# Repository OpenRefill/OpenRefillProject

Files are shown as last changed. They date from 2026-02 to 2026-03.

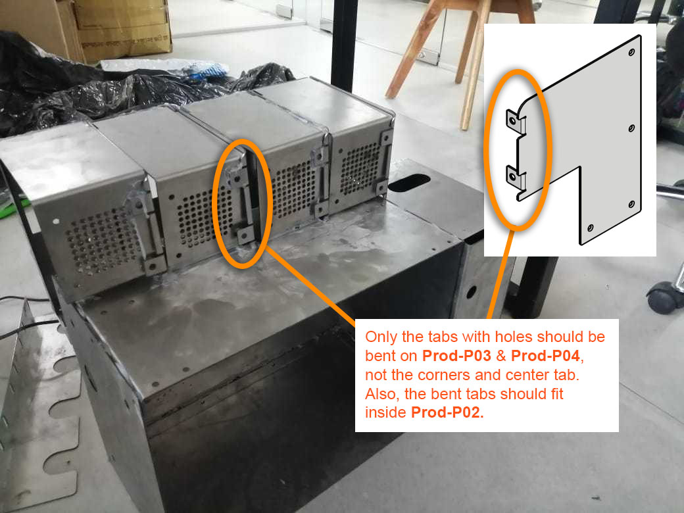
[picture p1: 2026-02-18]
Hardware Designs/Mechanical/Photos/img-20230101-wa0018 (with notes) copy.jpg

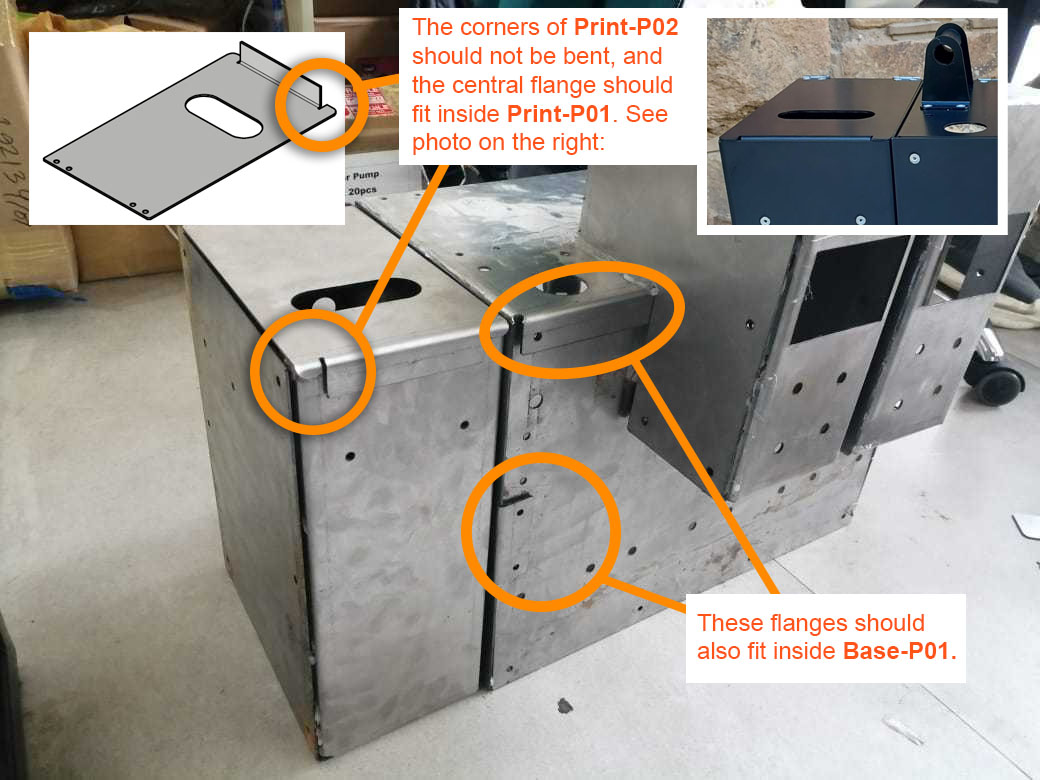
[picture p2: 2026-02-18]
Hardware Designs/Mechanical/Photos/img-20230101-wa0014 (with notes).jpg

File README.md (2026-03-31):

# OpenRefill 
An open-source platform for refill and reuse dispenser systems. 

## The Mission
We want to accelerate the shift away from single-use plastic by enabling open, low-cost refill dispensing systems, through open-source designs, shared standards, and collaboration. Our focus is on personal care products (shampoos, conditioners, soaps, etc) that are sold to developing markets in sachets. 

Find out more at [openrefill.com](https://openrefill.com) and dive deeper at our [research wiki](https://github.com/OpenRefill/OpenRefill/wiki/Research). 

## Getting started
1. Read the [licence notice](LICENCE-NOTICE.md) and understand your freedoms and responsibilities.
2. Read our [code of conduct](CODE_OF_CONDUCT.md) and our [contribution guidelines](CONTRIBUTING.md).
3. Check out our [discussions page](https://github.com/OpenRefill/OpenRefill/discussions). Feel free to introduce yourself in [Welcome to OpenRefill Discussions!](https://github.com/OpenRefill/OpenRefill/discussions/1#discussion-9450050).
4. Review our [open issues](https://github.com/OpenRefill/MainProject/issues) to start contributing.
5. Understand the logistics, operational, and business model dimensions of deploying a refill service by heading to [Refill Realities](https://www.refillrealities.com/#playbooks) and reading their playbooks. 

## Need help? 
- Email us at hello@openrefill.com.

## Follow Us 
[LinkedIn](https://www.linkedin.com/company/open-refill/?viewAsMember=true) 
#openrefill 
#refillrevolution

## Original Contributors

OpenRefill is a collaborative effort brought to life by industry leaders in smart logistics, digital innovation, and global sustainability:

* **[Smartfill](https://smartfill.store)** – A leading global supplier of smart dispensers and cloud-based logistics and inventory management for bulk products.
* **[DY|DX Digital](https://dydx.digital)** – A leading innovation consultancy.
* **[TRANSFORM](https://www.transform.global/home.html)** – A joint initiative between Unilever, the UK Foreign, Commonwealth & Development Office (FCDO), and EY.
* **[BOPINC](https://bopinc.org)** & **[Unilever Bangladesh](https://www.unilever.com.bd/)** – Strategic partners whose work on the **URefill** project provided foundational results for this initiative.
* **[Wizkit](https://www.linkedin.com/company/wizkitglobal/posts/?feedView=all)** - Wizkit supported the testing, deployment and maintenance of a fleet of machines in Dhaka stores during the initial **URefill pilots**.

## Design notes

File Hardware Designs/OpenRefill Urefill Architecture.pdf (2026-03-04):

# OpenRefill Technical Architecture:

## Urefill Version

2026/03/03

# Overview

The U-Refill cabinet contains 4 liquid personal care dispensers. Each dispenser has the following main components:
- 1x Peristaltic pump
- 1x LCD screen
- 4x Buttons
- 1x Trigger nozzle
- 1x Loadcell
- 1x Peripheral PCB

All the components are attached to the main cabinet, which consists of laser cut and bent metal parts. Some 3d-printed parts are also used, e.g., the button covers.

The dispenser functions as follows:
1. User selects an amount
2. User presses trigger button/nozzle upwards
3. The pump runs for a calibrated time period for the selected volume
4. A receipt is printed out.
5. The dispense event is sent to the cloud interface.

The dispenser load cell weighs the dispenser hopper (5L bottle or jerry can). The loadcell reading can be used to determine if the hopper is empty. Currently though the loadcell implementation is not functional and needs to be redesigned.

### Version History

This document pertains to the U-refill project version. A minor upgrade was manually made to improve the flow rate in 2024. Also an alternative and improved hopper bracket was designed, however not implemented during this time. The main PCB was also updated to include a ground plane. Previously it only had ground traces.

# Mechanical Components

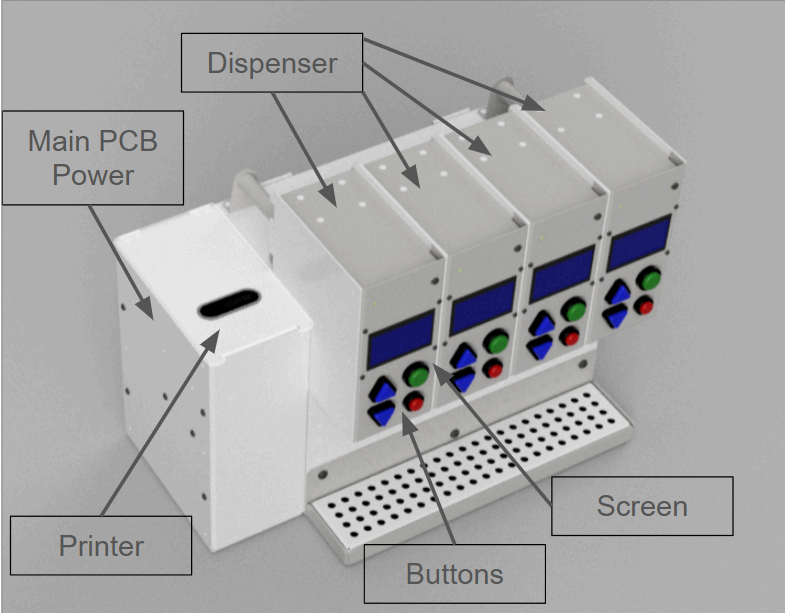
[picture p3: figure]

The cabinet has four dispensers, with a shared power supply, main PCB and printer.

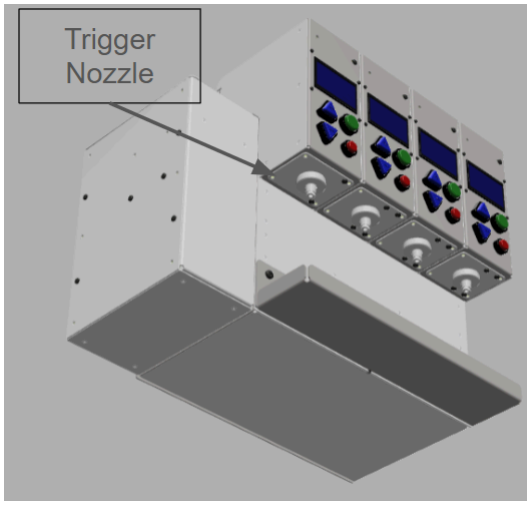
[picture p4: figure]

The trigger nozzle - this is pressed up to start dispensing after selecting an amount.

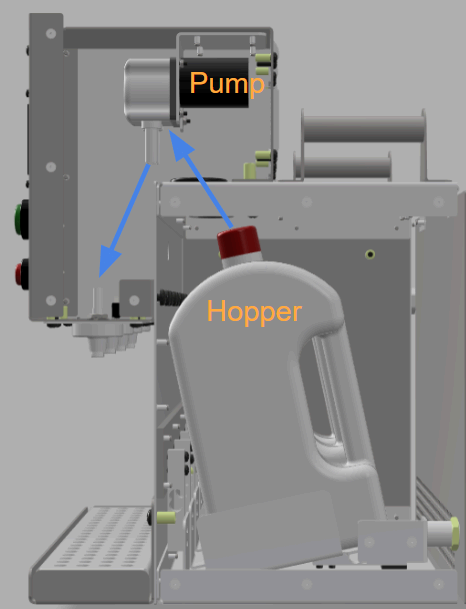
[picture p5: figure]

Side view of a dispenser. The hopper (5L jerrycan or bottle), contains the product supply. The motor pumps the liquid through the tube (blue arrows) to the Trigger Nozzle. Note this shows the updated design for the corrected load cell orientation.

# Electronics

The main PCB controls all four dispensers. The PCB has three ESP32 development boards. The boards communicate with each other using I2C.

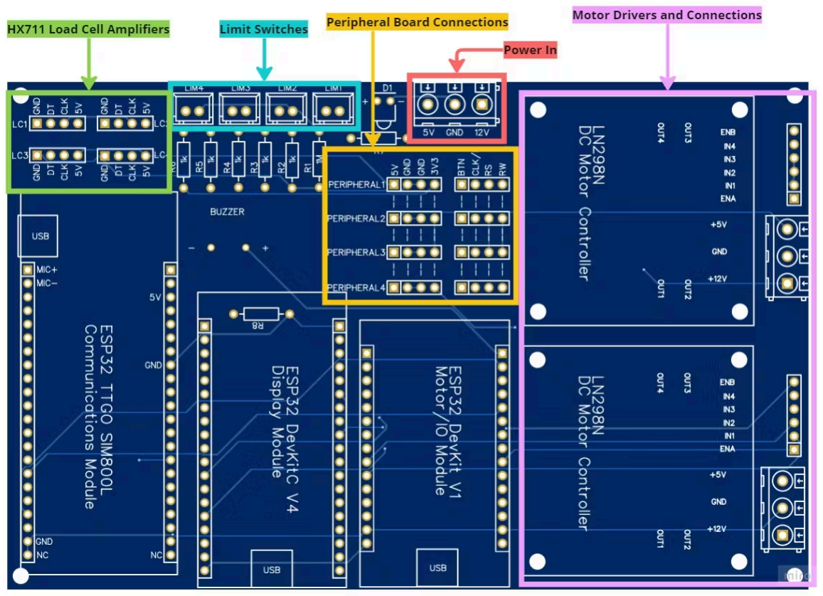
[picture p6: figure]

The main PCB with connection headers.

### Comms Module

Development Board: LILYGO TTGO T-Call V1.4 CH9102F QFN24 ESP32 Wireless Module GPRS Antenna SIM Card SIM800L Board

This ESP communicates with Azure-IoT-Central. The sim-card module mounted on it however does not work with the IoT/ESP internet library, and is not used. A WiFi router is used instead. Internet connection is used to send status updates and dispense events (records) to the cloud database. The current time is also obtained with NTP sync.

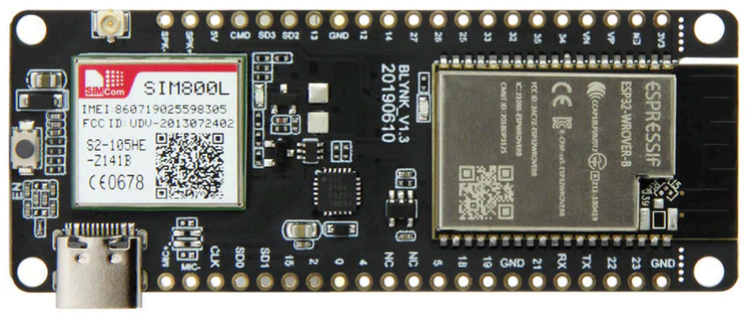
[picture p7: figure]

The LilyGo ESP module with SIM card slot

The loadcell ADC boards are also connected to this ESP. But as noted, the load cell circuit and mechanical orientation are not functional. The HX711 module (breakout board) is used to convert the load cell signal into a digital value using an ADC. The ADC digital output might need to be level shifted (5V to 3.3V).

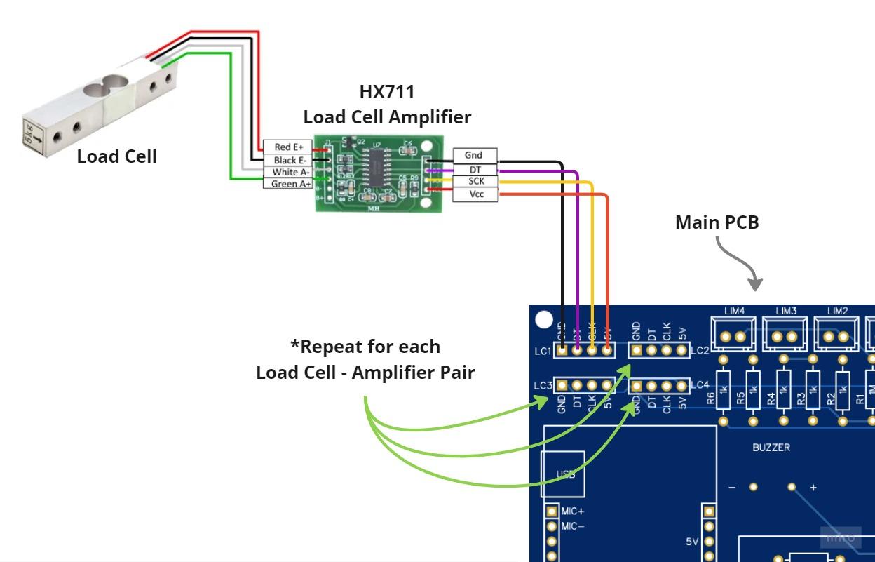
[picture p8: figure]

The loadcell connected to an HX711 loadcell ADC and amplifier, which is connected to the main PCB

### Display Module

Development Board: ESP32-WROOM32 DevKitC V4

This ESP drives all the displays. The display is a 128x64 LCD character display . Currently, the display is set to use only Bangladeshi characters.

The display module connects to each display with the Peripheral PCB.

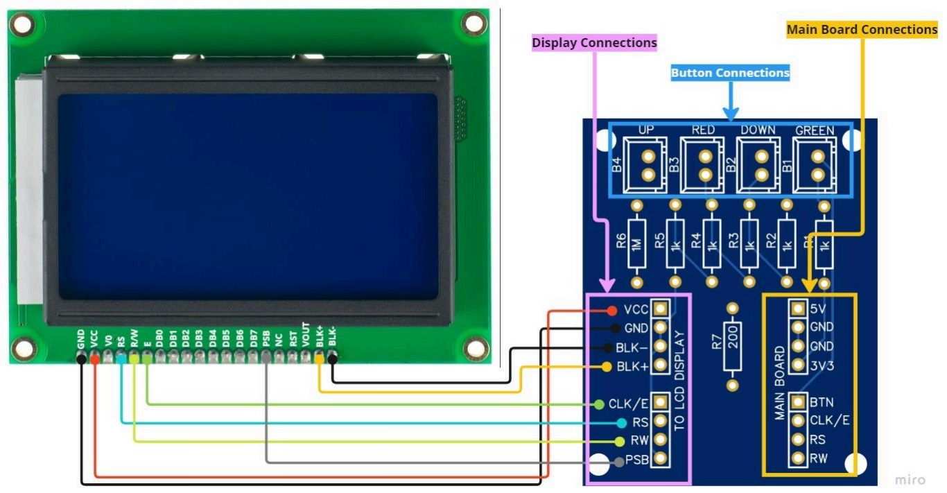
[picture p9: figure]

The display module connected to the peripheral PCB

### Main (Motor and IO) Module

Development Board: ESP32-WROOM32 DEVKIT V1

The main board does the following:
- Controls the four pump motors with DC motor drivers (also breakout boards).
- Check the buttons and trigger status of each dispenser. A resistor ladder is used to reduce the number of input pins required. All the buttons for one dispenser are connected to one pin. The voltage level as read with the ADC is used to determine if a specific button is pressed or not. The four nozzle-trigger buttons are also joined together using the same technique. The buttons are wired via the peripheral PCB to the main PCB.
- Control the buzzer.
- Connects to the Bluetooth printer to print receipts.

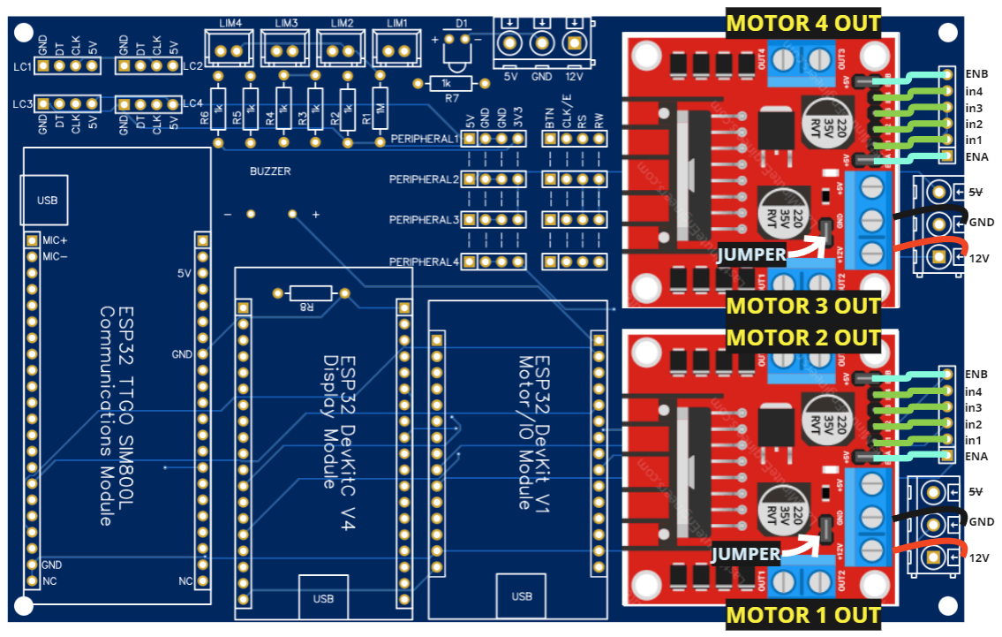
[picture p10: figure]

View of motor drivers mounted on the main PCB

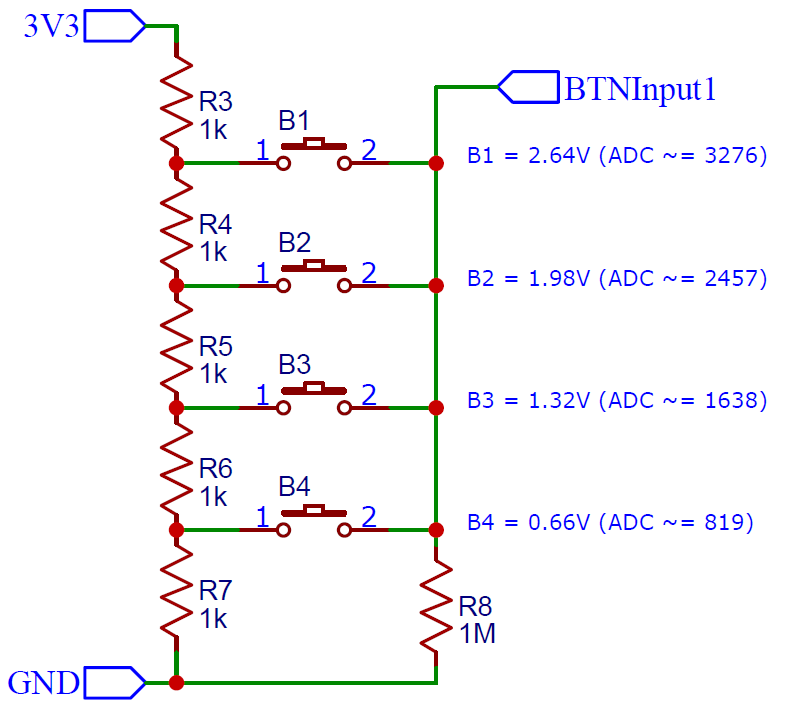
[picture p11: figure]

Voltage ladder used for buttons

### Pin Assignments: Peripheral PCB to Main Board

Pin Name | Pin Type | Description | Notes
5V | Power | 5V Power in
GND | Ground | Signal ground
3V3 | Analog Input | 3.3V reference for button circuit
BTN | Analog Output | Analog button voltage out
CLK/E | Serial Clock | Display clock
RS | Serial Data | Display chip select
R/W | Serial Data | Display data

### Pin Assignments: Peripheral to Display

Pin Name | Pin Type | Description | Notes
VCC | Power | 5V Power
GND | Ground | Signal ground
BLK- | Ground | Backlight cathode (-)
BLK+ | Power | Backlight anode (+)
CLK/E | Serial Clock | Display clock

RS | Serial Data | Display chip select
R/W | Serial Data | Display data
PSB | Digital Input | Parallel/Serial Bit (0=Serial)

## Power Supply

A 12V 10A (120W) power supply with battery connection is used to power the cabinet. A buck converter outputs the 5V power rail, which supplies the screens and ESP boards.

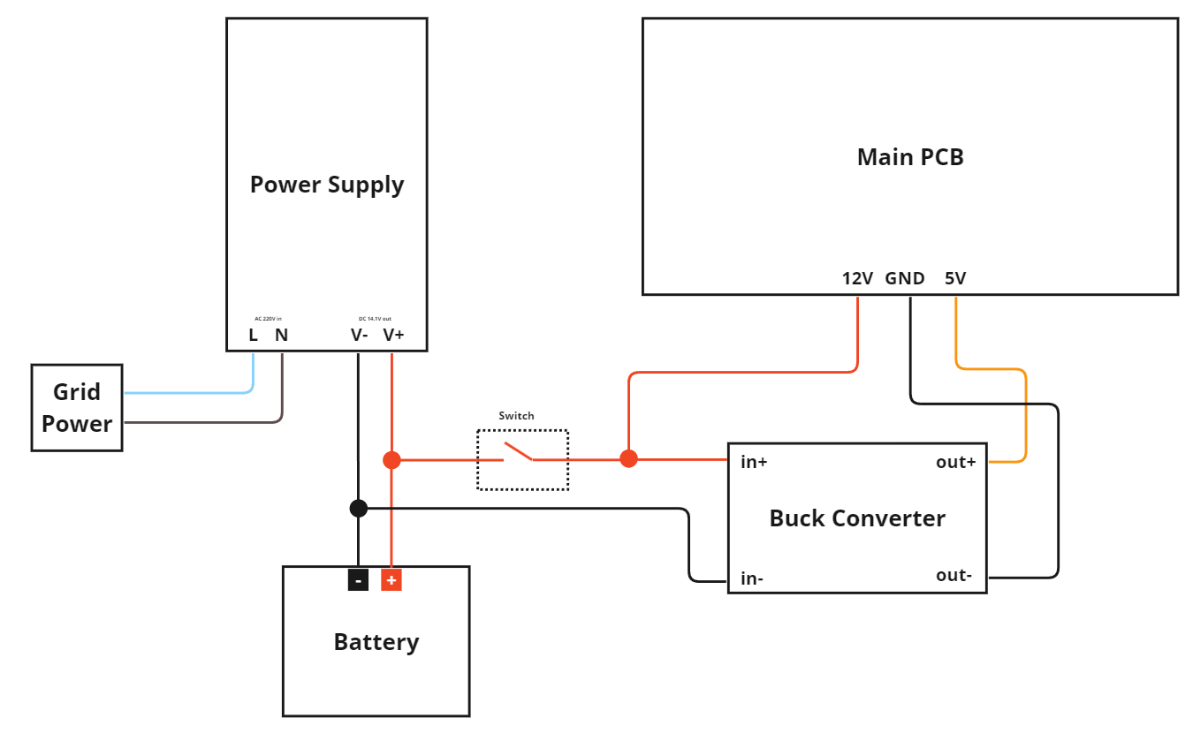
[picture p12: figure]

Block diagram of the power supply

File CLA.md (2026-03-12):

# OPENREFILL CONTRIBUTOR LICENCE AGREEMENT

Thank you for your interest in contributing to the OpenRefill project. 

To protect the project, its users, and the open-source community, Smartfill Ltd (UK company number 13799654) (**Smartfill**) requires all contributors to agree to this Contributor Licence Agreement before we can accept your contributions. 

This agreement ensures we have the necessary legal rights to distribute your contributions while you retain ownership of your original work. By submitting a contribution (for example, through a pull request, email, or issue tracker), you unconditionally and irrevocably agree to the following terms— 

## 1. DEFINITIONS 

1.1. **"You"** means the individual or legal entity submitting the Contribution; 

1.2. **"Contribution"** means any hardware design, software, firmware, documentation, or other material you submit to the OpenRefill project; and 

1.3. **"Project"** means the OpenRefill project, managed by Smartfill. 

## 2. GRANT OF RIGHTS 

You grant to Smartfill— 

2.1. a perpetual, worldwide, non-exclusive, royalty-free, irrevocable licence to reproduce, prepare derivative works of, publicly display, publicly perform, sublicense, and distribute your Contribution; and

2.2. a patent licence to make, have made, use, sell, offer for sale, and import your Contribution as incorporated into the Project.

## 3. YOUR RETAINED RIGHTS 

3.1. You retain all copyright and patent rights in your Contribution. 

3.2. This agreement does not prevent you from using your own Contribution for any other purpose or licensing it to others under different terms. 

## 4. OUTBOUND LICENSING 

Accepted Contributions may be distributed to the public under the project’s then-current opensource licensing framework (currently CERN-OHL-W-2.0, MPL-2.0, and CC-BY-SA-4.0). 

## 5. YOUR WARRANTIES 

By submitting a Contribution, you confirm and warrant— 

5.1. that you have the legal right to grant these licences; 

5.2. that the Contribution is your original creation, or you have sufficient rights and permissions from any third-party owners to make the submission and grant the rights in this agreement; and 

5.3. that, to the best of your knowledge, the Contribution does not include material subject to third-party licence terms that are inconsistent with the project’s open licensing framework (CERNOHL-W-2.0, MPL-2.0, and CC-BY-SA-4.0). 

## 6. DISCLAIMER OF WARRANTIES 

Except for the warranties stated in **Section 5** above, you provide your Contribution on an "AS IS" basis, without any additional warranties or conditions, express or implied. 

## 7. ACCEPTANCE:

By submitting a pull request or transferring project files to Smartfill, you explicitly accept and agree to the terms of this agreement.

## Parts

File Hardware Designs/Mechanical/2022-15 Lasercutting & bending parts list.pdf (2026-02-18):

Part Number | Part Title | Operation | Material | Material Thickness | Finish | QTY | Part Drawing No:
Base-P01 | Base Box Face | Cut | Mild steel | 1,6 | As supplied | 10 | 2022-15-D01
Base-P02 | Base Box Top | Cut, bend | Mild steel | 1,6 | As supplied | 10 | 2022-15-D02
Base-P03 | Base Box Bottom | Cut, bend | Mild steel | 1,6 | As supplied | 10 | 2022-15-D03
Base-P04 | Base Box Right | Cut, bend | Mild steel | 1,6 | As supplied | 10 | 2022-15-D04
Base-P05 | Base Box Left | Cut, bend | Mild steel | 1,6 | As supplied | 10 | 2022-15-D05
Base-P06 | Base Box Door | Cut | Mild steel | 1,6 | As supplied | 10 | 2022-15-D06
Base-P07 | Mounting Plate | Cut | Mild steel | 5,0 | As supplied | 10 | 2022-15-D07
Base-P08 | Alignment Bracket | Cut, bend | Mild steel | 1,6 | As supplied | 10 | 2022-15-D08
Base-P09 | Hopper Support | Cut, bend | Mild steel | 2,0 | As supplied | 40 | 2022-15-D09
Hand-P01 | Handle Bracket | Cut, bend | Mild steel | 1,6 | As supplied | 40 | 2022-15-D10
Noz-P03-1 | Nozzle Mount (Pin) | Cut | Mild steel | 1,6 | As supplied | 40 | 2022-15-D11
Noz-P04 | Switch Mount | Cut | Mild steel | 1,6 | As supplied | 40 | 2022-15-D13

### Dispenser Sheet Metal Cutting & Bending Parts List

Print-P01 | Printer Box Main | Cut, bend | Mild steel | 1,6 | As supplied | 10 | 2022-15-D14
Print-P02 | Printer Box Side | Cut | Mild steel | 1,6 | As supplied | 10 | 2022-15-D15
Print-P03 | Printer Box Top | Cut, bend | Mild steel | 1,6 | As supplied | 10 | 2022-15-D16
Print-P04 | Printer Bracket | Cut, bend | Mild steel | 2,0 | As supplied | 10 | 2022-15-D17
Prod-P01 | Product Box Face | Cut, bend | Mild steel | 1,6 | As supplied | 40 | 2022-15-D18
Prod-P02 | Product Box Cover | Cut, bend | Mild steel | 1,6 | As supplied | 40 | 2022-15-D19
Prod-P03 | Product Box Right | Cut, bend | Mild steel | 1,6 | As supplied | 40 | 2022-15-D20
Prod-P04 | Product Box Left | Cut, bend | Mild steel | 1,6 | As supplied | 40 | 2022-15-D21
Prod-P05 | Pump bracket | Cut, bend | Mild steel | 2,0 | As supplied | 40 | 2022-15-D22
Tray-P01 | Tray support | Cut, bend | 304 Stainless | 2,0 | Brushed | 10 | 2022-15-D24
Tray-P02 | Drip Cover | Cut, bend | 304 Stainless | 1,6 | Brushed | 10 | 2022-15-D25
Hand-P02 | Handle Tube | Cut | Mild steel, (round tube) | 1,6 | As supplied | 20 | 2022-15-D26
Base-P10 | Cam Lock Catch | Cut, bend | Mild steel, (round tube) | 2,0 | As supplied | 10 | 2022-15-D27

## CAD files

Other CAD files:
Hardware Designs/Mechanical/Drawings/DWG/Dispenser Overall Dimensions.dwg
Hardware Designs/Mechanical/Drawings/DWG/4 product dispenser unit -3.dwg
Hardware Designs/Mechanical/Drawings/DWG/Drip container - request for quotes.dwg
Hardware Designs/Mechanical/Drawings/DWG/Short printer box.dwg
Hardware Designs/Mechanical/Drawings/DWG/Other Parts Drawings.dwg
Hardware Designs/Mechanical/Drawings/DWG/Overview drawings D01-03.dwg
Hardware Designs/Mechanical/Drawings/DWG/external dimensions for cardboard.dwg
Hardware Designs/Mechanical/Drawings/DWG/Tall printer box.dwg

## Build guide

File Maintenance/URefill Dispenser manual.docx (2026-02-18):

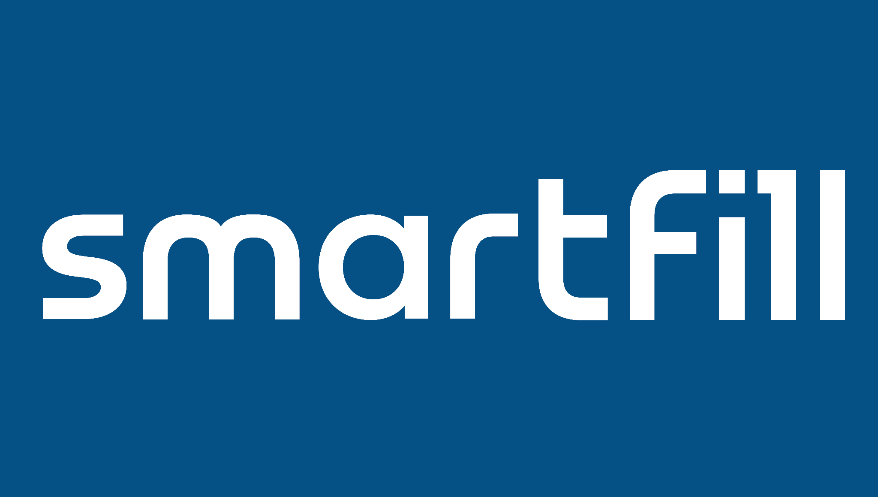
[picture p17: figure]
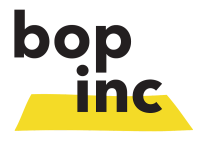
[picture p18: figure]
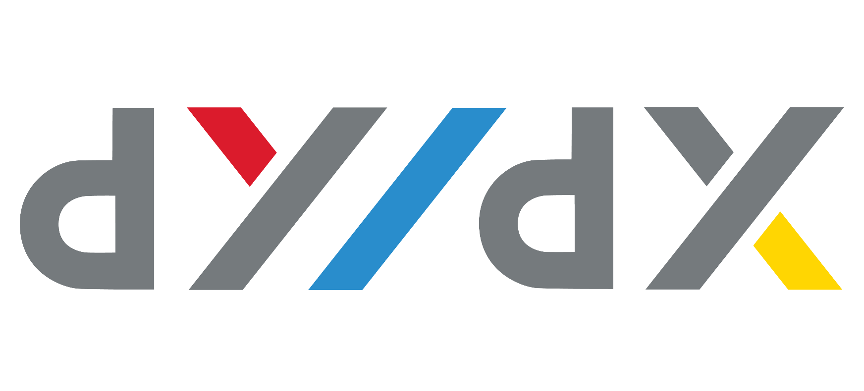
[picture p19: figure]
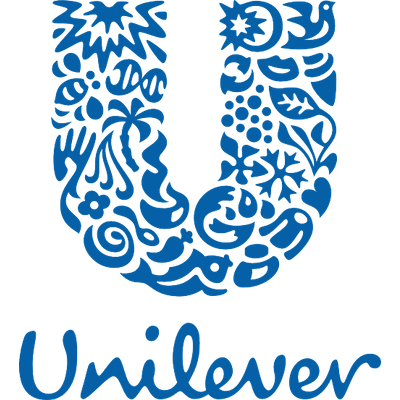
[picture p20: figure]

Bopinc

Personal Care Dispenser Manual

Version 1.0

05 December 2022

## Contents

Contents 2

Background 3

Dispenser Overview 3

Power supply 3

Measurements and Key Components 3

Dispensing Accuracy 5

Product Quality Assurances 5

Usage 5

Stock replenishment 7

Troubleshooting 8

## Background

The refill dispenser is an electronic machine that dispenses viscous liquid personal care products such as shampoo. Consumers use the machine to fill empty, reusable containers with product from the dispenser. The objective of the dispenser is to encourage shoppers to reduce the purchasing and use of personal care products in small plastic sachets which have become an environmental problem.

## Dispenser Overview

### Power supply

Electricity is required for the electronic refill dispenser to operate. There is no on/off switch for the dispenser and it automatically turns on once connected to a power supply, and off when there is no power supply. The machine is indicated as being on when the LCD screens show text and intermittently flash with light.

The dispenser has a standard cable and plug that plugs into the main grid electricity supply. In the case of brief periods of electricity loss, there is a battery that is able to power the dispenser for up to 4 hours of continual motor use, and it is charged by the main power supply.

### Measurements and Key Components

Front view

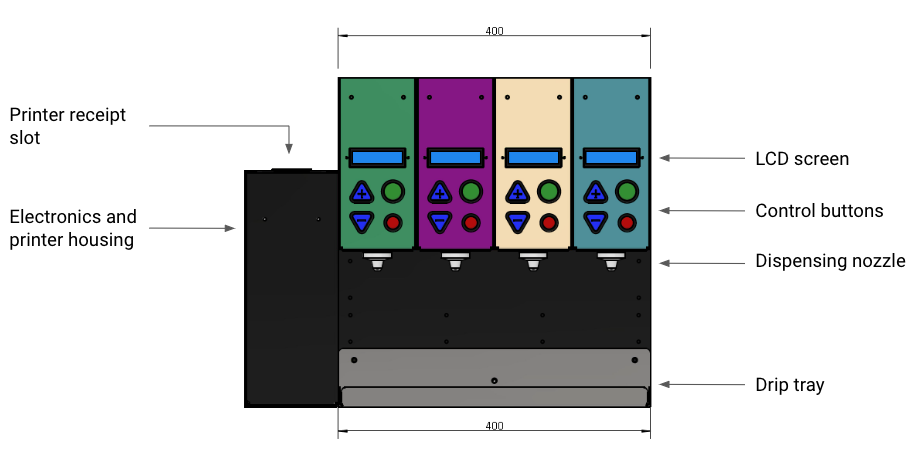
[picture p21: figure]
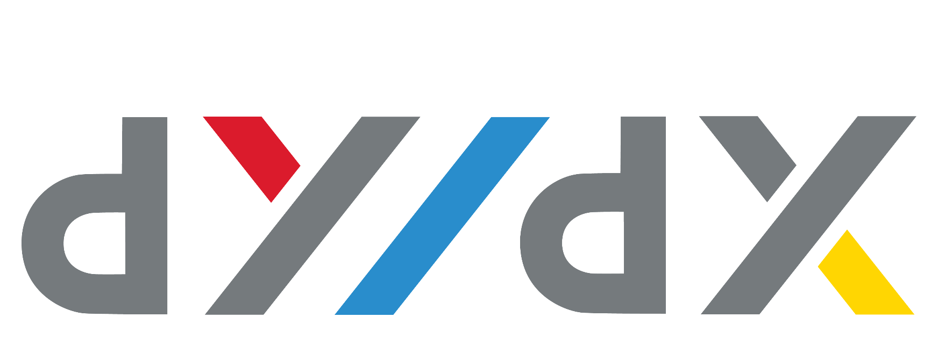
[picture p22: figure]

Side view

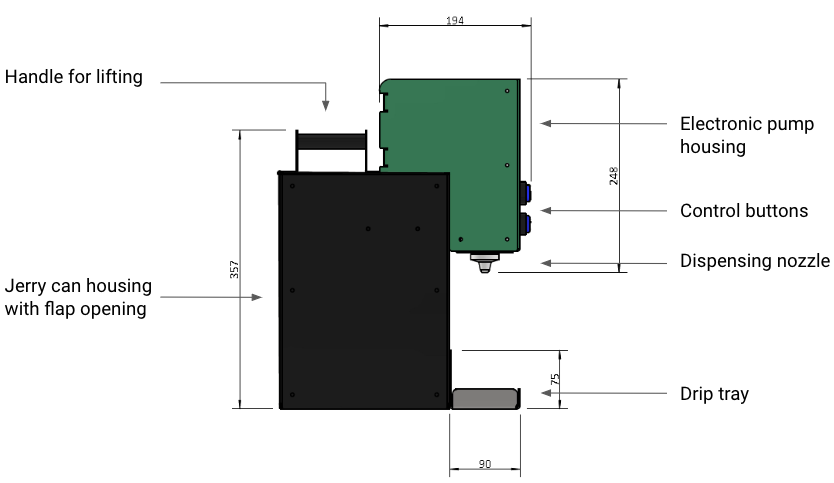
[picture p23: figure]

Internal view

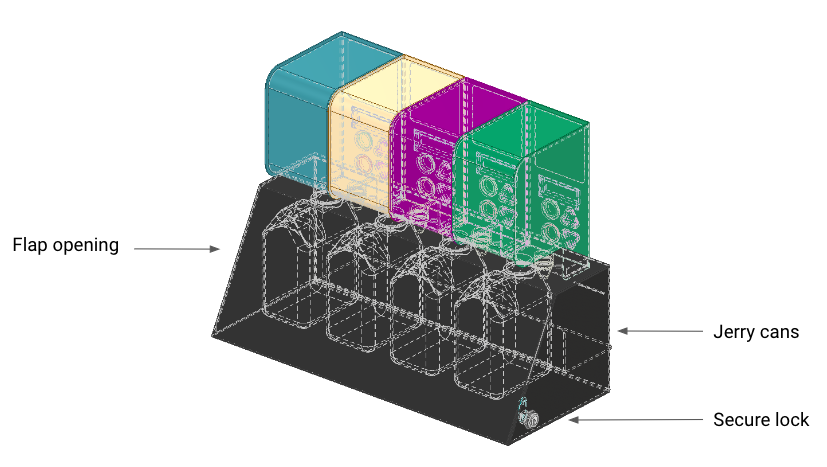
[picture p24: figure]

### Dispensing Accuracy

Because of the small quantities dispensed by the machine, the refill station is very accurate with an error margin of less than 3%. Any error will be positive (i.e. more product dispensed rather than less), so the customer gets at least the quantity they select.

### Product Quality Assurances

Product quality is maintained in 4 ways:

1. Jerry cans are securely contained within the dispenser itself, and access to the jerry cans are protected by lock and key. Only approved Unilever contacts have a key and are able to gain access to the jerry cans to protect the product from being tampered with.
2. Jerry cans are not exposed to UV as they are secured within the dispenser.
3. To avoid any microbial contamination or degradation of the product itself, the dispenser can only dispense product from the jerry cans, product cannot be reversed back into the machine or jerry cans.
4. To minimise product contact with air as well as unintentional dripping of the product, the dispenser nozzle contains a seal closure that shuts when the machine stops dispensing.

## Usage

To use the machine, a consumer will use a reusable, empty plastic container that can be filled with the product, used at home, and washed once empty to refill again.

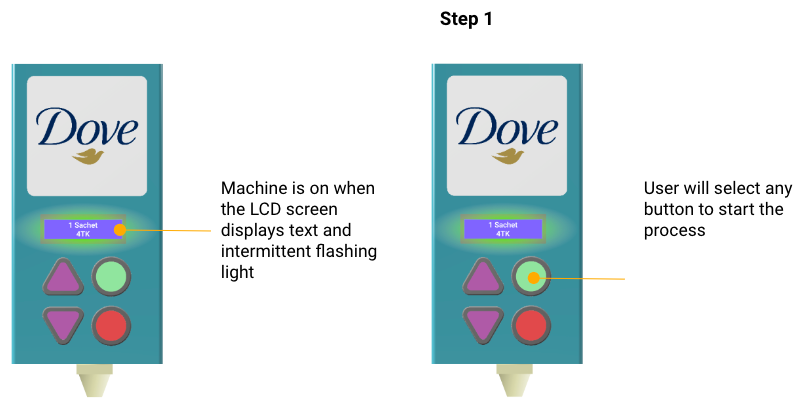
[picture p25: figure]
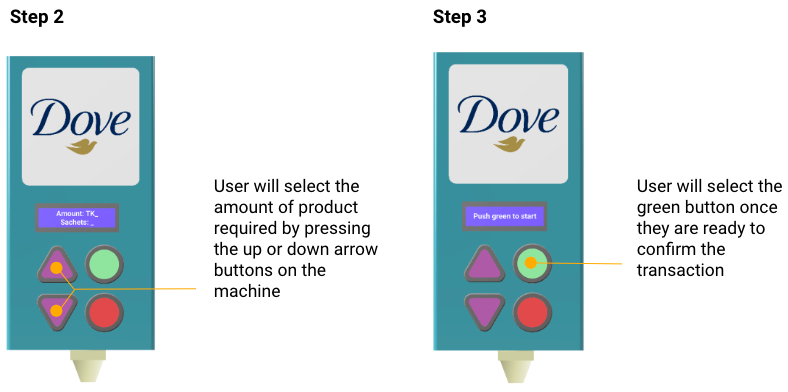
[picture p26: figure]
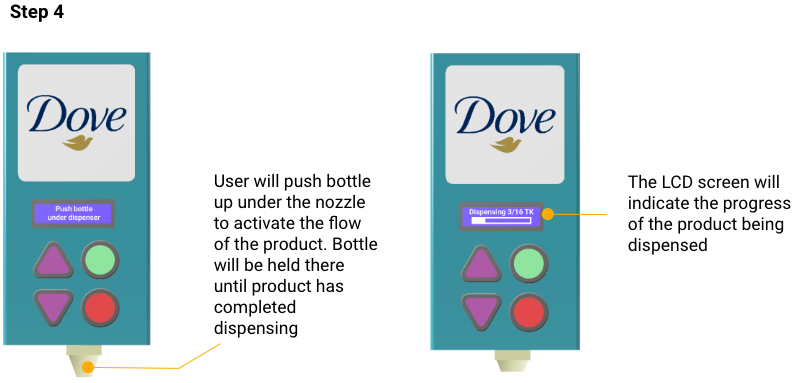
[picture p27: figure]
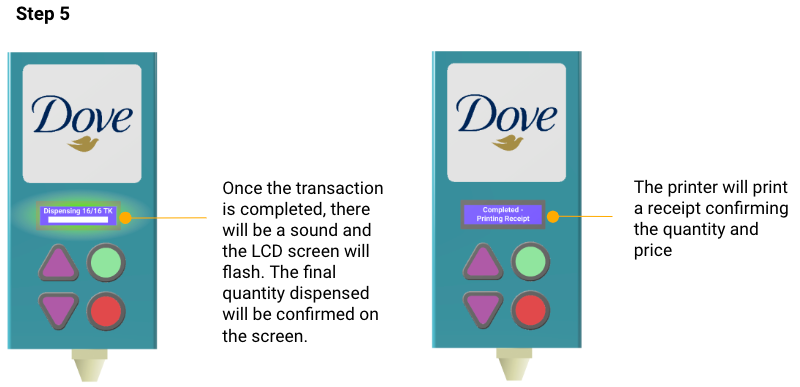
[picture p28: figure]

## Stock replenishment

Unilever brand representatives are responsible for replenishing empty jerry cans, and will have a key to unlock the refill dispenser to gain access to replenish jerry cans.

Product stock levels are monitored via cloud software where weekly stock and usage reports will be circulated with Bopinc and Wizkit teams. Jerry cans with low stock levels will be flagged by the software, and teams can notify Unilever to order and facilitate replenishment of that machine and product.

The process to replenish empty jerry cans is as follows:

1. Authorised persons will unlock the dispenser opening with a key and lifting the back flap to gain access to the jerry cans
2. The lid of the jerry can will be unscrewed, and the jerry can removed from the dispenser housing
3. The tube and nozzle of the product being replenished will undergo cleaning as per Unilever requirements
4. The lid of the new, full jerry can will be removed, the dispenser tube will be placed into the new jerry can and the attached cap will be screwed on
5. The jerry can will be placed securely within the dispenser housing
6. The housing flap will be closed and the lock secured with a key

## Troubleshooting

If the dispenser stops working, the retailer can notify Unilever who will contact their technical partner, Wizkit, to troubleshoot the machine on site. The machine can be replaced with a back-up machine if any issues cannot be immediately resolved, and the broken dispenser can be repaired as needed offsite.

Personal Care Dispenser Manual | Version 1.0

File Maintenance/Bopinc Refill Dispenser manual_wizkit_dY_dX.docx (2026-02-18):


Bopinc

Personal Care Dispenser Manual

Version 1.1

16/08/2023

## Contents

Contents 2

1. Background 2

2. Usage 3

3. Dispenser Overview 4

Power supply 4

Measurements and Key Components 5

4. How dispensing works in the backend 5

Dispensing Accuracy 5

Identification, Networking, and Data Collection 8

Product Quality Assurances and Cleaning 8

5. Stock replenishment 9

6. Troubleshooting 10

## 1. Background

The refill dispenser is an electronic machine that dispenses viscous liquid personal care products such as hand soap and shampoo. Consumers use the machine, located at small neighborhood stores, to refill a reusable plastic container with their favorite personal care products from the dispenser. The objective of the dispenser is to give consumers an affordable alternative to purchasing personal care products in single-use plastic sachets which have become an environmental problem in markets like Bangladesh. The refill machine is designed and manufactured by Wizkit, DYDX, and Bopinc, in consultation with Unilever Bangladesh which will be piloting this innovation at a small number of Dhaka.

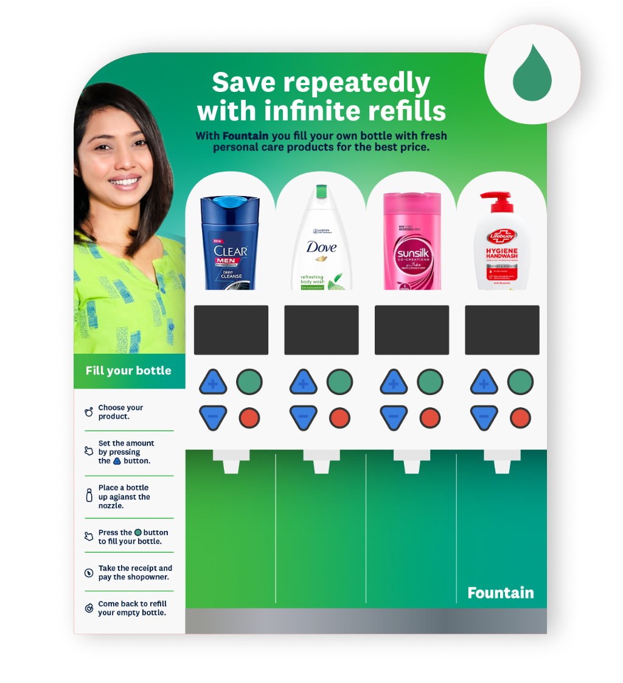
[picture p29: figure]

Image: Frontside of the personal care dispenser (in Bangladesh, text on the artwork will be translated to Bengali)

## 2. Usage

To use the machine, a consumer will bring a reusable, empty plastic container to the store where the dispenser is located. Either the retailer or the user will operate the machine to refill the container with the product of choice. Consumers get a printed receipt and pay the retailer, after which they take the bottle, use the product at home, and wash the bottle once it is empty and needs to be refilled again.

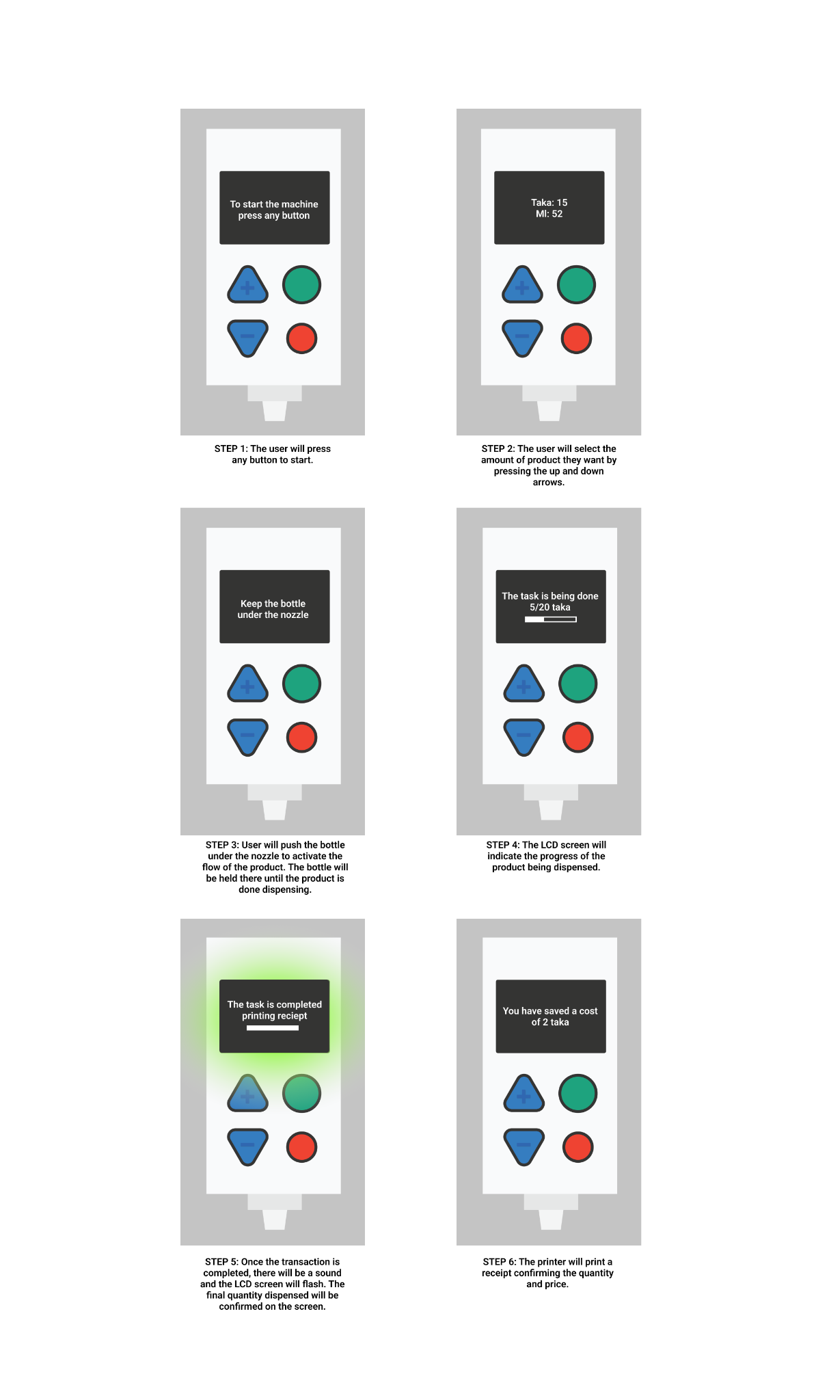
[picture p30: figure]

## 3. Dispenser Overview

### Power supply

Grid power is required for the electronic refill dispenser to operate. There is no on/off switch for the dispenser; it automatically turns on once connected to a power supply and off when there is no power supply. The machine is indicated as being on when the LCD screens show text and light are lit up. Additionally the machine will make a distinct buzzer sound when the machine is initialized and ready to dispense.

The dispenser has a standard power cable and a plug that plugs into the main grid electricity supply. In the case of brief periods of power blackouts, the battery inside the machine can continue to power the dispenser for up to 4 hours of continual motor use. The battery is recharged when the main power supply is back on.

Electric connection

The machine works at a Maximum of 12V, 5 A and can be plugged into a normal electricity plug point. Maximum power output is 60W.

The machine operates at less than half of its specified wattage so the actual power consumption is around 0.03 Wh

Everyday cost for the machine's electricity will be around 4 Taka (considering 10 hours of shop open time and unit price as 9.5 Taka).

Battery

The battery is 7Ah battery which can provide a maximum backup of 84Wh which would result in about 4-5 hours of backup power

### Measurements and Key Components

Front view

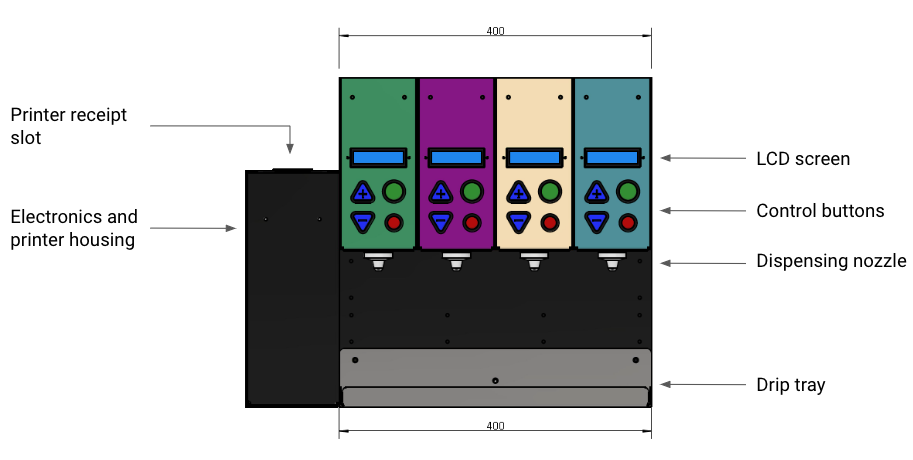
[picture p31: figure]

Side view


Internal view


## 4. How dispensing works in the backend

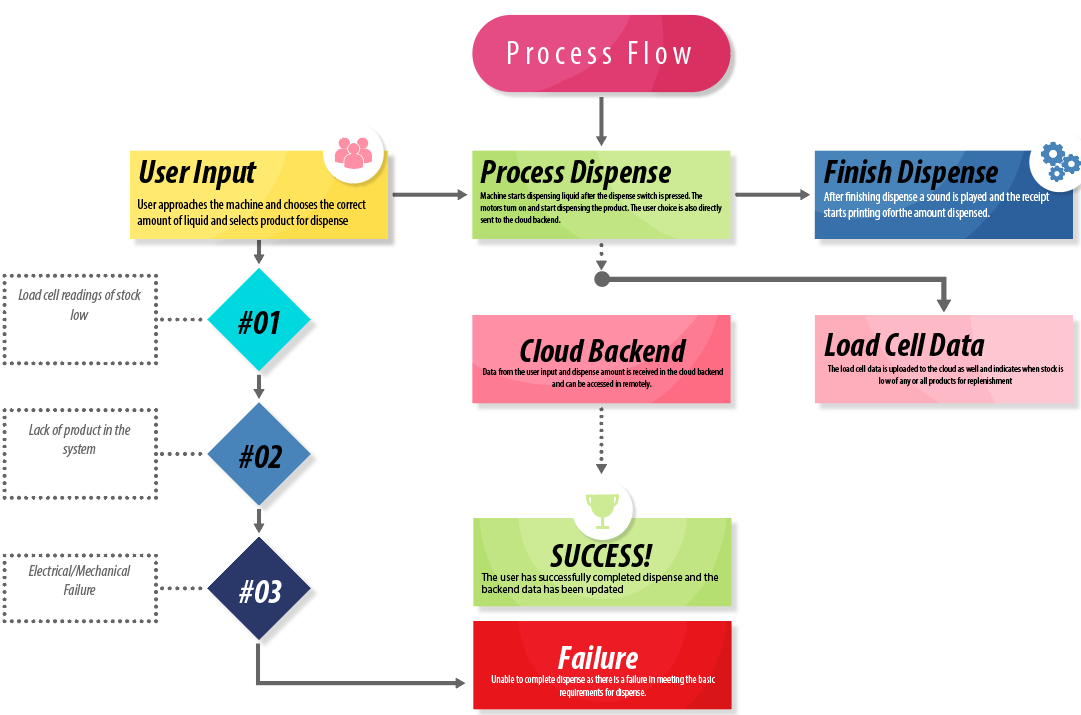
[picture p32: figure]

### Dispensing Accuracy

The dispenser provides three options of volume for the user to choose. The options reflect low, medium and high values where the medium value generally represents the most commonly dispensed amount. Error margin of the dispenser is between an under dispense of 3% to an over dispense of maximum 10% . Any error is designed generally tol be advantageous for the consumer, meaning they get a bit more than the quantity they select provided external factors do not greatly affect the integrity of the fluids in the machine.

The machine uses 4 peristaltic pumps rated at 12V, 500ml/min controlled by a precise L298N motor driver to dispense accurate amounts of fluid. Fluid accuracy is ensured during the initial calibration of the machine which runs the specific liquids multiple times through the system until the system is calibrated to dispense exactly or slightly more than the requested amount by the user. Each product segment hosts a separate motorized unit and each product category is individually calibrated to dispense the correct amount.

Calibration Methods:

1. Dispense Calibration To calibrate for dispensing the motor is run for a predetermined set amount of time after priming to check how much liquid is dispensed using a graduated cylinder/beaker. Once the relationship with timing and amount dispensed is established the dispensing factor inside the microcontroller of the machine is set to always dispense accurate amounts of fluid. These motors are industrially used as dosing pumps and therefore are known for high levels of accuracy which does not waiver over time.
2. Load-Cell Calibration

A known load is placed on the holder which is mounted to the load cell. The known weight is used to calibrate the sensor and then that calibration factor is uploaded to the microcontroller through code using a computer. The load cell mainly helps to report low stock and allows it to stop dispensing when stock is below a threshold value as per what is set in the system.

### Identification, Networking, and Data Collection

Every machine is connected to the internet via a unique sim-card and machine ID. This allows the creators to identify and track each machine by its geographical location, network timing, connectivity, and also by its unique ID (a personalized number for each machine). When a machine is first set up in a specific location, the machine is initialized by our technical team to connect it to the cloud services. Once connected, the machine can report forms of machine usage data to the cloud server. Data includes number of user interaction per day, dispensing amount, time of dispensing, and machine downtime. The machine does not collect data specific to individual customers, meaning all data is anonymous. The data that is captured is solely used for the purpose of monitoring and evaluation of how the machines perform.

### Product Quality Assurances and Cleaning

Quality of the personal care products dispensed is maintained in 4 ways:

1. Suppliers restock the machines using jerry cans that are securely contained within the dispenser itself. Access to the jerry cans is protected by lock and key. Only approved Unilever brand representatives have a key and are able to gain access to the jerry cans to protect the product from being tampered with.
2. Jerry cans are not exposed to UV as they are secured within the dispenser.
3. To avoid any microbial contamination or degradation of the product itself, the dispenser can only dispense the product from the jerry cans, the product cannot be reversed back into the machine or jerry cans.
4. To minimize product contact with air as well as unintentional dripping of the product, the dispenser nozzle contains a sealed closure that shuts when the machine stops dispensing.
5. The nozzle of the machine can be wiped clean using a damp cloth, possibly with ethanol. This is important because consumers will touch the nozzle with their refill container.

Cleaning

Regular and frequent cleaning of the nozzles is recommended to stop buildup around the nozzles. This can be achieved by using isopropyl alcohol or ethanol and a disposable tissue/paper tower to clean the nozzle head.

Deeper cleaning must only be carried out by authorized Unilever restocking personnel where a standard cleaning process must be followed:

1. Unplug the machine and remove the tubing from the jerry cans carefully.
2. Clean the exterior of the tubing with isopropyl alcohol/ethanol
3. Turn the machine on and connect the tubing to isopropyl alcohol/ethanol containers
4. Dispense the liquid using the regular machine function until the liquid starts coming out from the nozzle. Once the liquid has come out from the nozzle stop dispensing on that unit and repeat for all 4 units within one machine.
5. Use a cotton bar or fiber cloth to clean the nozzle head with alcohol/ethanol.
6. Use distilled water to clear out any excess alcohol/ethanol from the system to avoid any other contamination.
7. Replenish product jerry cans and put the tubing inside the product jerry cans (make sure the tubing does not touch other parts of the machine during the process after cleaning.)
8. Close and lock the access door of the machine.

## 5. Stock replenishment

Unilever brand representatives are responsible for replenishing empty jerry cans and will have a key to unlock the refill dispenser to gain access to replenish jerry cans. Product stock levels are monitored via cloud software where weekly stock and usage reports will be circulated with Bopinc and Wizkit. The software will flag Jerry cans with low stock levels, and teams can notify Unilever to order and facilitate replenishment of that machine and product.

The process to replenish empty jerry cans is as follows:

1. Authorized persons to unlock the dispenser by opening it with a key and lifting the back flap to gain access to the jerry cans.
2. Unscrew the lid of the jerry cans and take the jerry cans out of the dispenser housing.
3. Clean the tube and the nozzle of the product that is being replenished as per the requirements described in section 4.
4. Remove the lid of the new, full jerry can and place the dispenser tube into the new jerry can, and screw the attached cap.
5. Place the jerry cans securely within the dispenser housing.
6. Close the housing flap and lock it with a key.

## 6. Troubleshooting

If the dispenser stops working, the retailer can notify Unilever who will contact their technical partner, Wizkit, to troubleshoot the machine on-site. The machine can be replaced with a backup machine if any issues cannot be immediately resolved, and the broken dispenser can be repaired as needed offsite.

Common Troubleshooting Scenarios:

Problems | Primary Actions | Secondary Actions | Advanced Diagnosis
Printer not printing | Check if the printer is on and the blue light on the printer is on. | Hold the power button to restart the printer | - Printer battery failure - Paper run out - Printer malfunction - Communication problem with communication ESP
| Check printer paper | Reload Printer Paper and restart the printer using the power button
Displays not turned on | Check main power line | Restart device. And Re-seat the power plug and check if the display comes on. | - Wiring fault - LCD damage - Voltage issues - Damaged microcontrollers - Power supply fault
| Hear to check sound feedback | Restart the device. If there is sound feedback but no display report immediately.
Buttons not working | Restart the device. | Restart using a different power outlet, and check to see if that specific power outlet has grounded. | - Grounding problem - Wiring fault
Random characters on screen | Restart device. | Make sure the device is on a stable surface and not moving or jerking constantly. | - Wiring Problem - Microcontroller damage
Uneven dispensing | Clean pipes and nozzle | Run a cleaning solution through the dispense delivery system. | - Nozzle clog - Silicone pipe damage
Premature stop while dispensing | Check product stock | Check for clogs. Run a cleaning solution through the system. | - Motor driver - Motor - Low stock - Microcontroller damage

Personal Care Dispenser Manual | Version 1.0

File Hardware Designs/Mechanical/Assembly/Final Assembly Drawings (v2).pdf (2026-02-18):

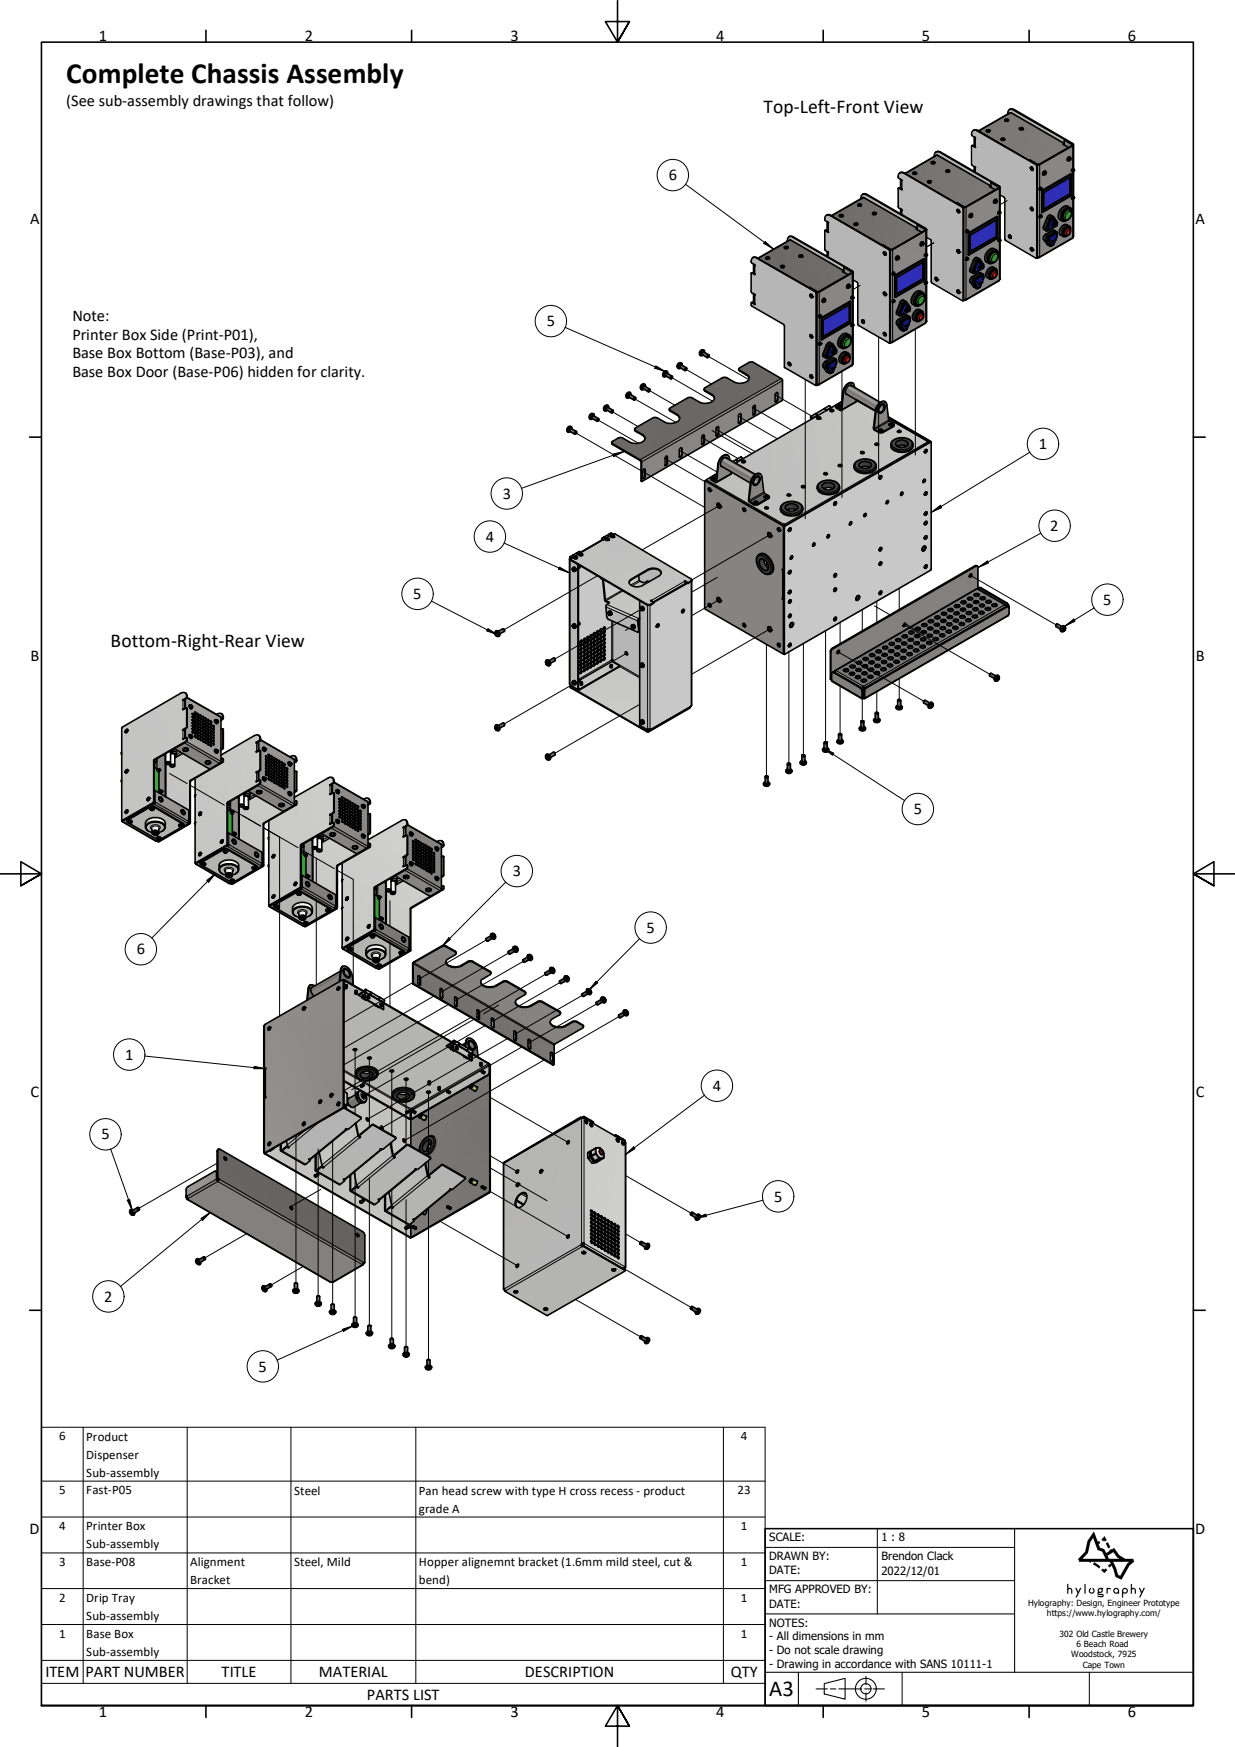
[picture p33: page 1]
Pan head screw with type H cross recess - product; grade A; Printer Box; Hopper alignemnt bracket (1.6mm mild steel, cut &; Alignment; Steel, Mild; Drip Tray; Base Box; PARTS LIST; ITEM PART NUMBER; TITLE; MATERIAL; DESCRIPTION; QTY; Brendon Clack

Complete Chassis Assembly

(See sub-assembly drawings that follow)

Top-Left-Front View

Note:
Printer Box Side (Print-P01),
Base Box Bottom (Base-P03), and
Base Box Door (Base-P06) hidden for clarity.

Bottom-Right-Rear View

SCALE:
DRAWN BY:
MFG APPROVED BY:
DATE:
NOTES:
- All dimensions in mm
- Do not scale drawing
- Drawing in accordance with SANS 10111-1

Hylography: Design, Engineer Prototype
https://www.hylography.com/

302 Old Castle Brewery
6 Beach Road
Woodstock, 7925
Cape Town

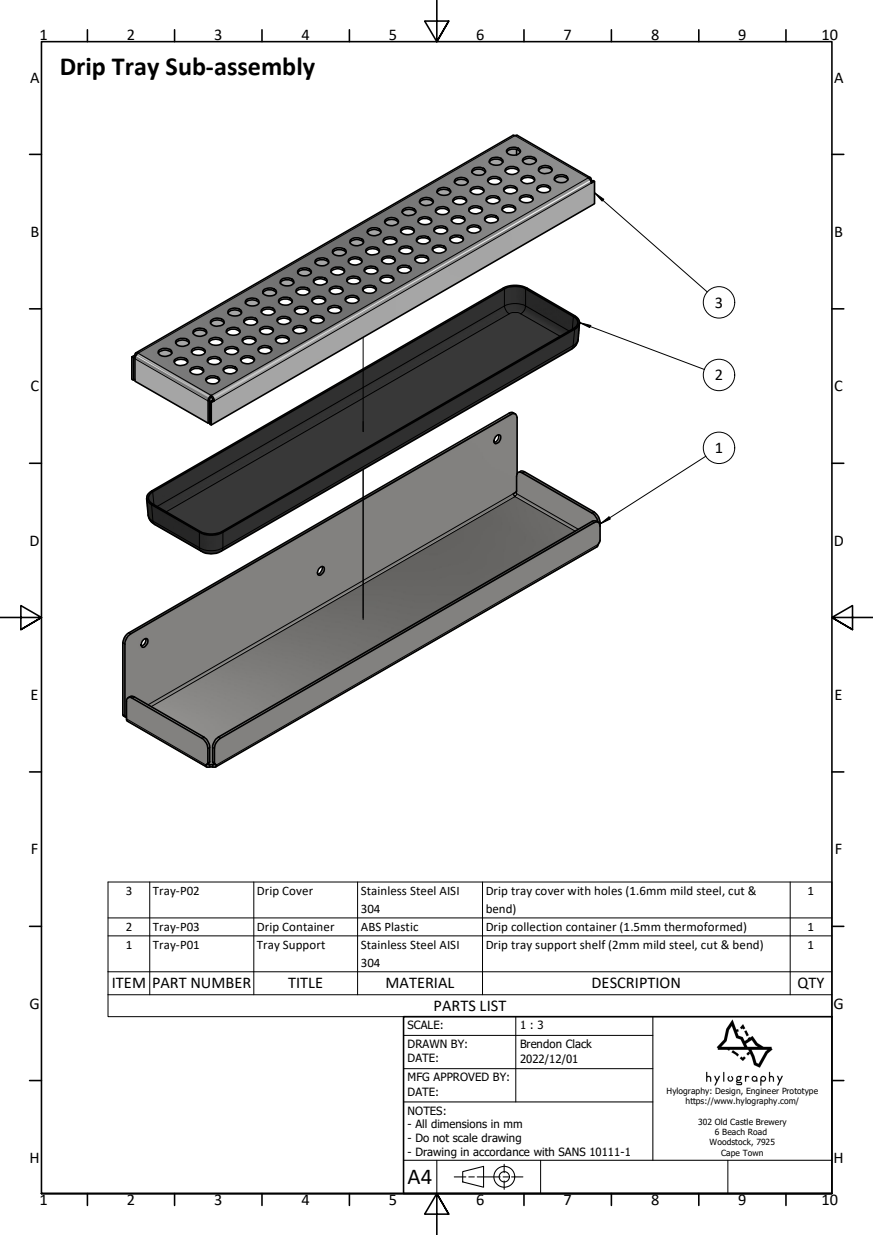
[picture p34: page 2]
PARTS LIST

Drip Tray Sub-assembly

3 | Tray-P02 | Drip Cover | Stainless Steel AISI 304 | Drip tray cover with holes (1.6mm mild steel, cut & bend) | 1

2 | Tray-P03 | Drip Container | ABS Plastic | Drip collection container (1.5mm thermoformed) | 1
1 | Tray-P01 | Tray Support | Stainless Steel AISI 304 | Drip tray support shelf (2mm mild steel, cut & bend) | 1

ITEM | PART NUMBER | TITLE | MATERIAL | DESCRIPTION | QTY

SCALE: | 1 : 3 | Hylography: Design, Engineer Prototype https://www.hylography.com/302 Old Castle Brewery
DRAWN BY: DATE: | Brendon Clack 2022/12/01

MFG APPROVED BY: DATE:

NOTES:
- All dimensions in mm

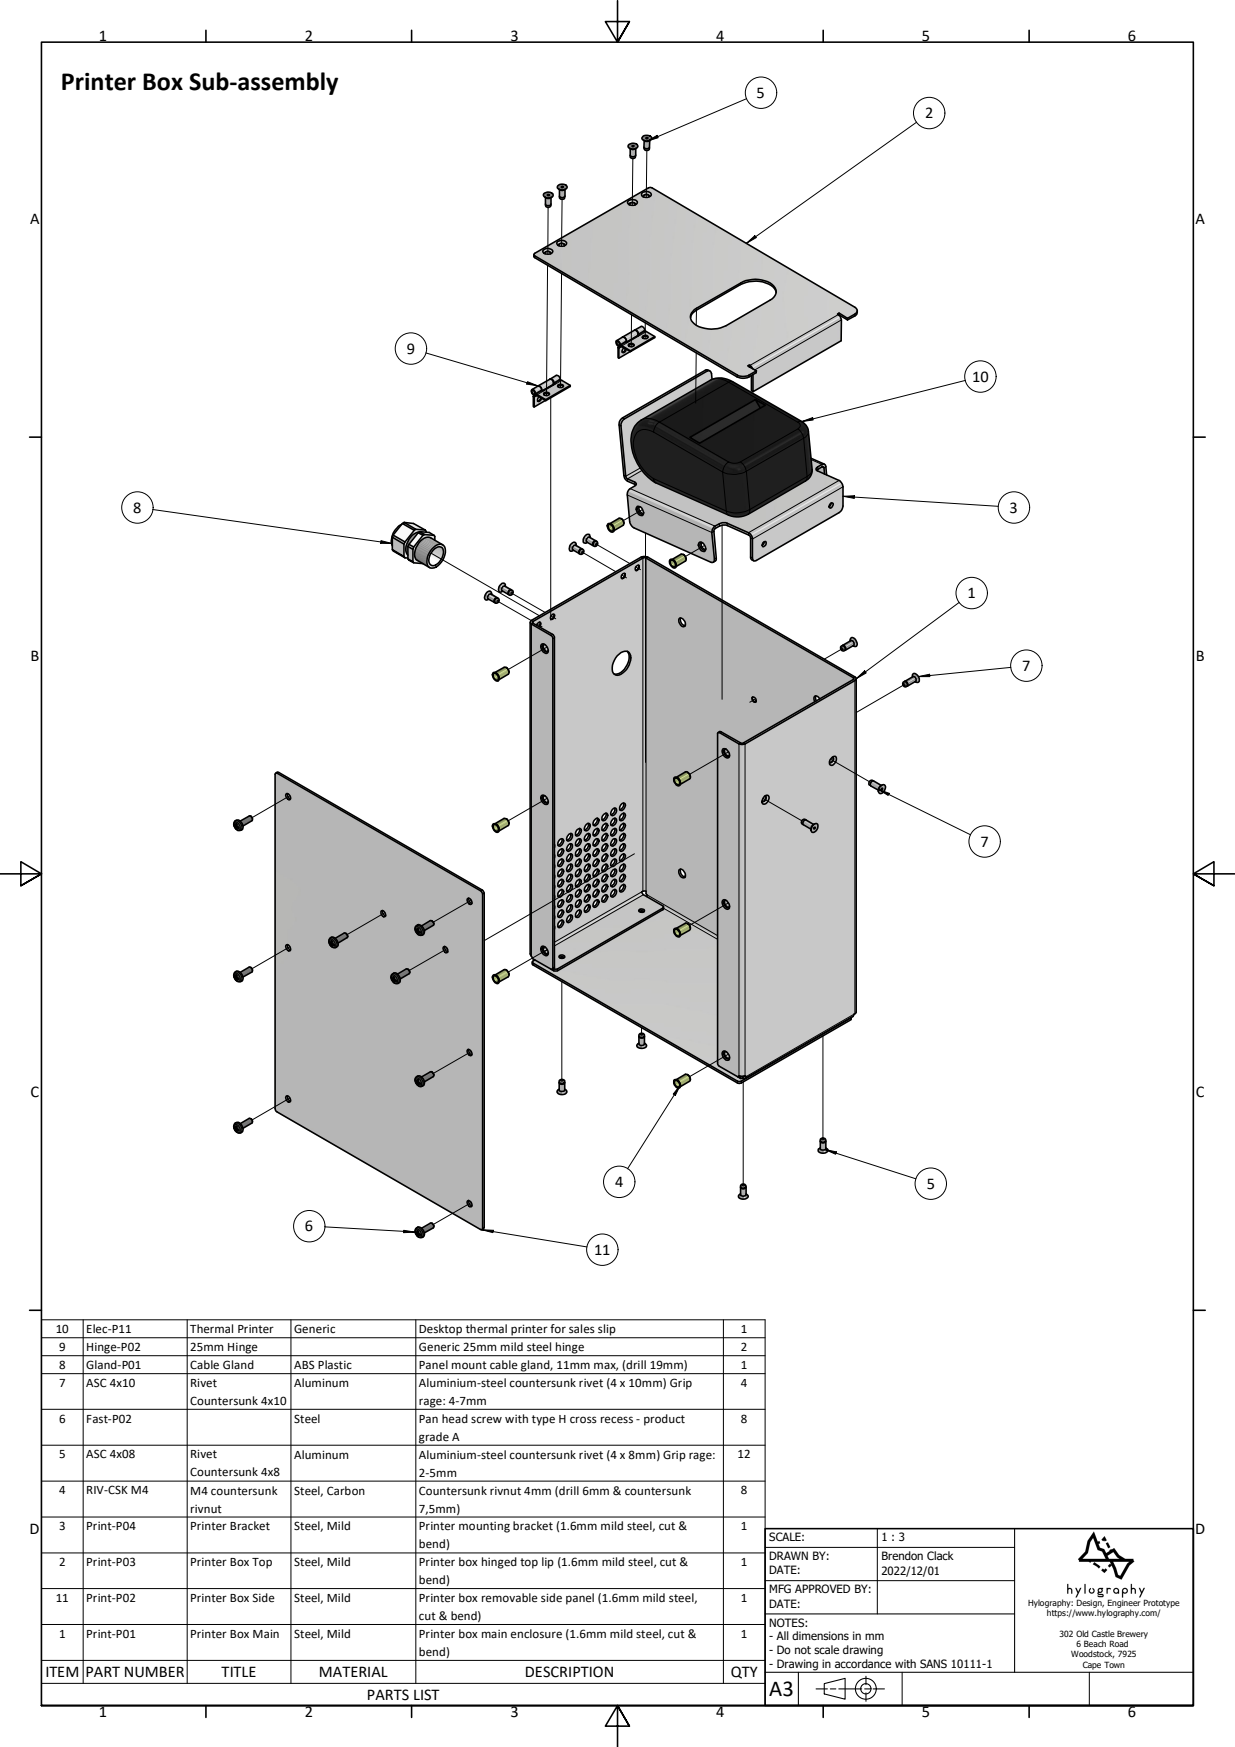
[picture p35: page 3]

Printer Box Sub-assembly

10 | Elec-P11 | Thermal Printer | Generic | Desktop thermal printer for sales slip | 1
9 | Hinge-P02 | 25mm Hinge | | Generic 25mm mild steel hinge | 2
8 | Gland-P01 | Cable Gland | ABS Plastic | Panel mount cable gland, 11mm max, (drill 19mm) | 1
7 | ASC 4x10 | Rivet Countersunk 4x10 | Aluminum | Aluminium-steel countersunk rivet (4 x 10mm) Grip rage: 4-7mm | 4

6 | Fast-P02 | | Steel | Pan head screw with type H cross recess - product grade A | 8

5 | ASC 4x08 | Rivet Countersunk 4x8 | Aluminum | Aluminium-steel countersunk rivet (4 x 8mm) Grip rage: 2-5mm | 12

4 | RIV-CSK M4 | M4 countersunk rivnut | Steel, Carbon | Countersunk rivnut 4mm (drill 6mm & countersunk 7,5mm) | 8

3 | Print-P04 | Printer Bracket | Steel, Mild | Printer mounting bracket (1.6mm mild steel, cut & bend) | 1

SCALE: | 1 : 3
DRAWN BY: DATE: | Brendon Clack 2022/12/01

2 | Print-P03 | Printer Box Top | Steel, Mild | Printer box hinged top lip (1.6mm mild steel, cut & bend) | 1

MFG APPROVED BY:

11 | Print-P02 | Printer Box Side | Steel, Mild | Printer box removable side panel (1.6mm mild steel, cut & bend) | 1

1 | Print-P01 | Printer Box Main | Steel, Mild | Printer box main enclosure (1.6mm mild steel, cut & bend) | 1

ITEM | PART NUMBER | TITLE | MATERIAL | DESCRIPTION | QTY

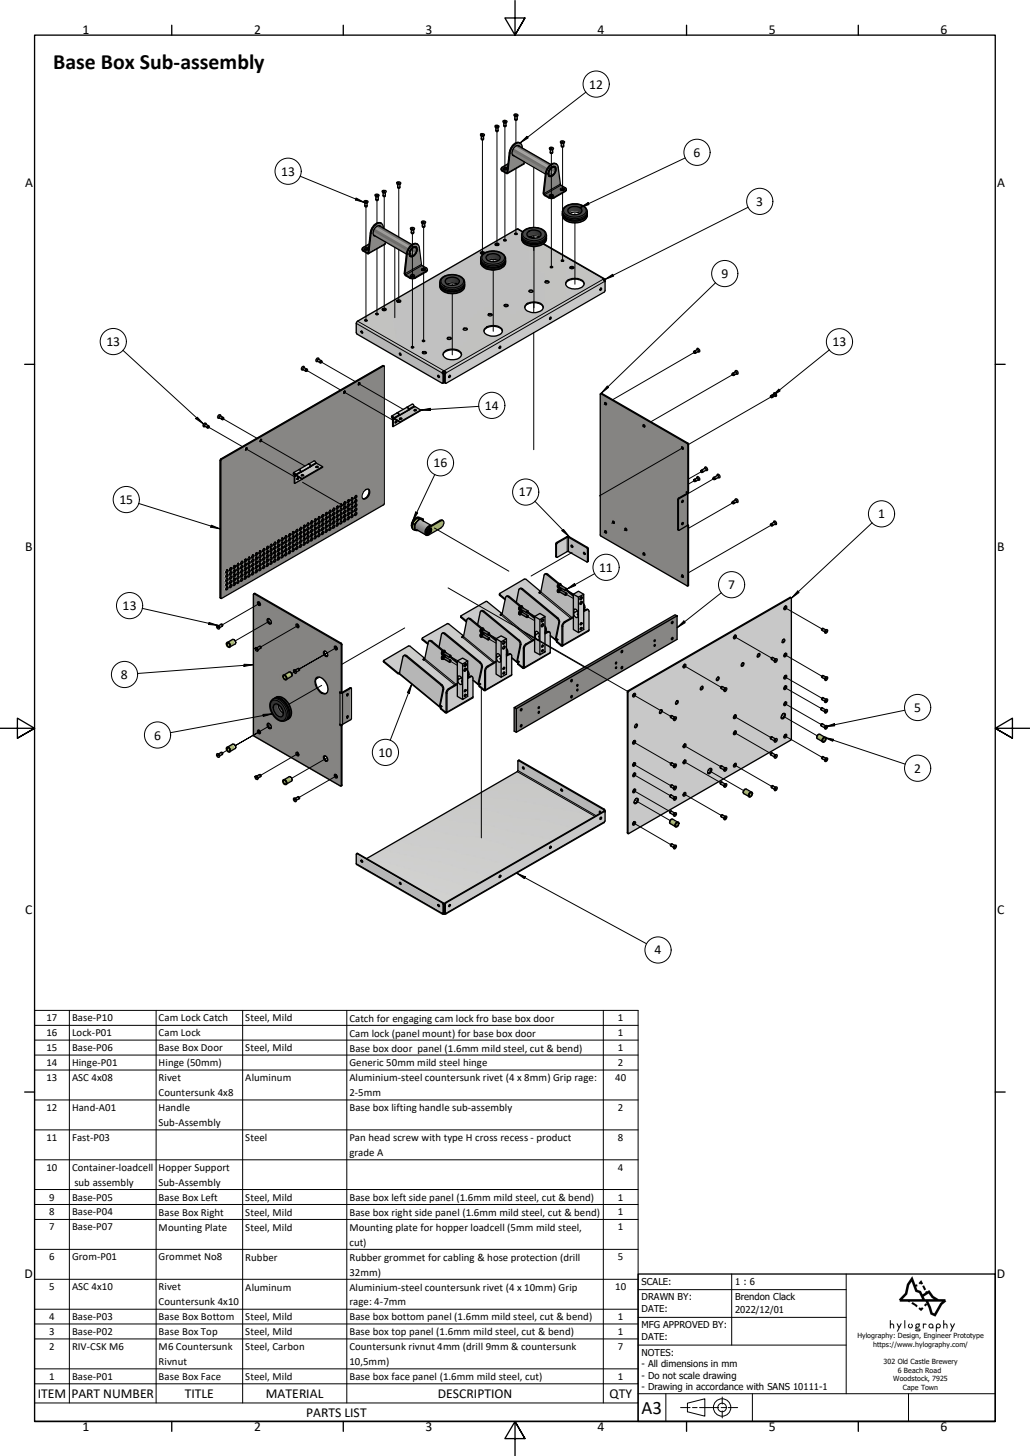
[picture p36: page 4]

Base Box Sub-assembly

17 | Base-P10 | Cam Lock Catch | Steel, Mild | Catch for engaging cam lock fro base box door | 1
16 | Lock-P01 | Cam Lock | | Cam lock (panel mount) for base box door | 1
15 | Base-P06 | Base Box Door | Steel, Mild | Base box door panel (1.6mm mild steel, cut & bend) | 1
14 | Hinge-P01 | Hinge (50mm) | | Generic 50mm mild steel hinge | 2
13 | ASC 4x08 | Rivet Countersunk 4x8 | Aluminum | Aluminium-steel countersunk rivet (4 x 8mm) Grip rage: 2-5mm | 40

12 | Hand-A01 | Handle Sub-Assembly | | Base box lifting handle sub-assembly | 2

11 | Fast-P03 | | Steel | Pan head screw with type H cross recess - product grade A | 8

10 | Container-loadcell sub assembly | Hopper Support Sub-Assembly | | | 4

9 | Base-P05 | Base Box Left | Steel, Mild | Base box left side panel (1.6mm mild steel, cut & bend) | 1
8 | Base-P04 | Base Box Right | Steel, Mild | Base box right side panel (1.6mm mild steel, cut & bend) | 1
7 | Base-P07 | Mounting Plate | Steel, Mild | Mounting plate for hopper loadcell (5mm mild steel, cut) | 1

6 | Grom-P01 | Grommet No8 | Rubber | Rubber grommet for cabling & hose protection (drill 32mm) | 5

5 | ASC 4x10 | Rivet Countersunk 4x10 | Aluminum | Aluminium-steel countersunk rivet (4 x 10mm) Grip rage: 4-7mm | 10

SCALE: | 1 : 6
DRAWN BY: DATE: | Brendon Clack 2022/12/01

4 | Base-P03 | Base Box Bottom | Steel, Mild | Base box bottom panel (1.6mm mild steel, cut & bend) | 1
3 | Base-P02 | Base Box Top | Steel, Mild | Base box top panel (1.6mm mild steel, cut & bend) | 1
2 | RIV-CSK M6 | M6 Countersunk Rivnut | Steel, Carbon | Countersunk rivnut 4mm (drill 9mm & countersunk 10,5mm) | 7

MFG APPROVED BY:

1 | Base-P01 | Base Box Face | Steel, Mild | Base box face panel (1.6mm mild steel, cut) | 1
ITEM | PART NUMBER | TITLE | MATERIAL | DESCRIPTION | QTY

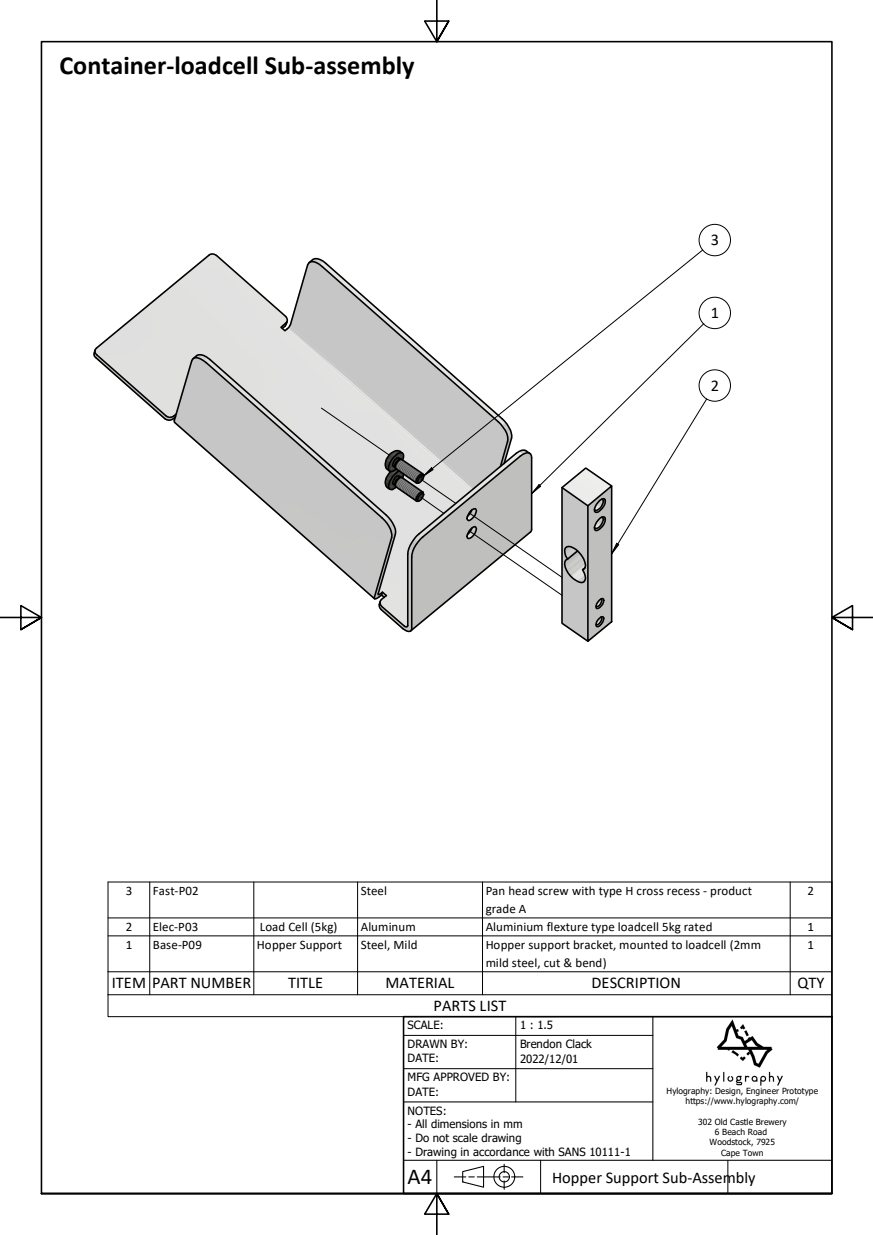
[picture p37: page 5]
PARTS LIST

Container-loadcell Sub-assembly

3 | Fast-P02 | | Steel | Pan head screw with type H cross recess - product grade A | 2

2 | Elec-P03 | Load Cell (5kg) | Aluminum | Aluminium flexture type loadcell 5kg rated | 1
1 | Base-P09 | Hopper Support | Steel, Mild | Hopper support bracket, mounted to loadcell (2mm mild steel, cut & bend) | 1

ITEM | PART NUMBER | TITLE | MATERIAL | DESCRIPTION | QTY

SCALE: | 1 : 1.5 | Hylography: Design, Engineer Prototype https://www.hylography.com/302 Old Castle Brewery
DRAWN BY: DATE: | Brendon Clack 2022/12/01

MFG APPROVED BY: DATE:

NOTES:
- All dimensions in mm

Hopper Support Sub-Assembly

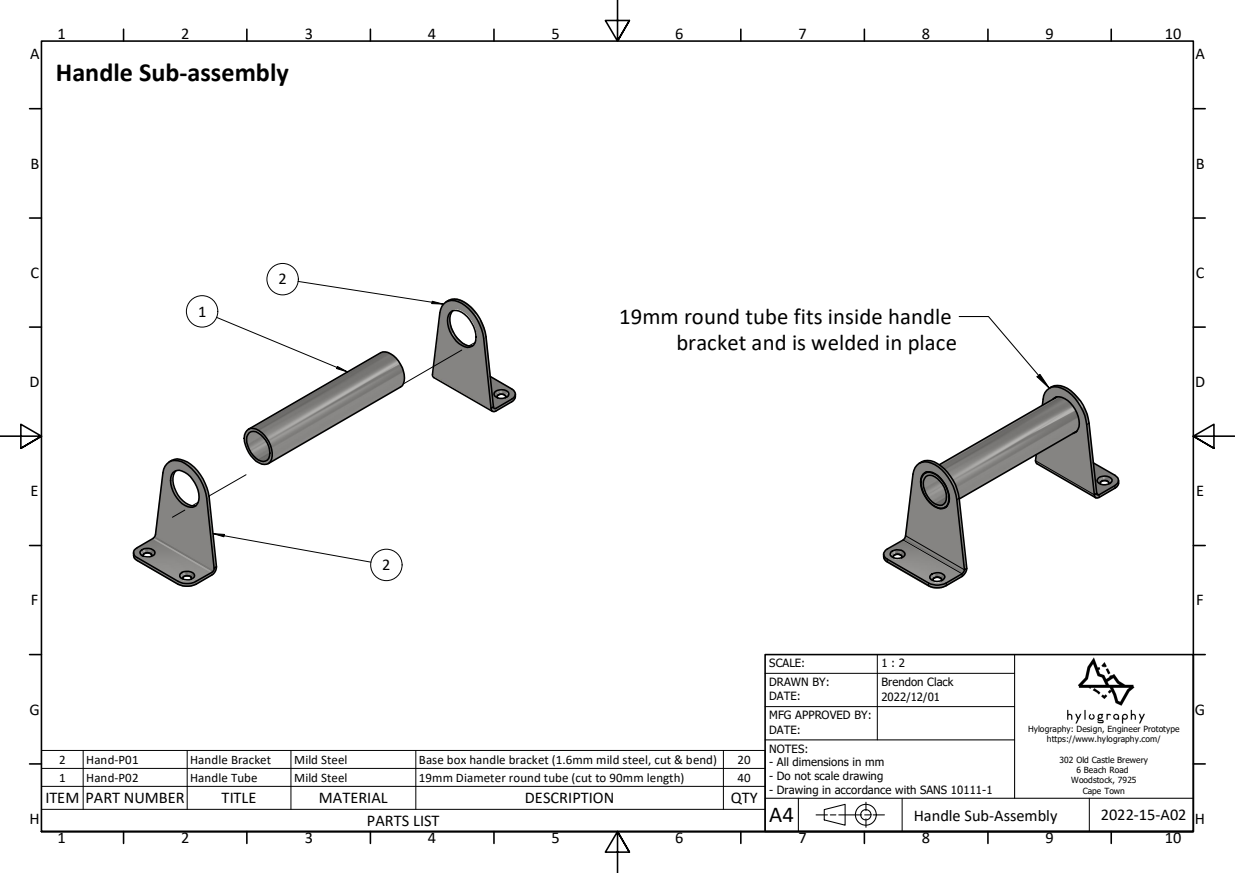
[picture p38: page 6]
Handle Sub-Assembly

Handle Sub-assembly

19mm round tube fits inside handle
bracket and is welded in place

DRAWN BY: DATE: | Brendon Clack 2022/12/01

MFG APPROVED BY: DATE:

Hylography: Design, Engineer Prototype
https://www.hylography.com/

NOTES:
- All dimensions in mm
- Do not scale drawing
- Drawing in accordance with SANS 10111-1

2 | Hand-P01 | Handle Bracket | Mild Steel | Base box handle bracket (1.6mm mild steel, cut & bend) | 20
1 | Hand-P02 | Handle Tube | Mild Steel | 19mm Diameter round tube (cut to 90mm length) | 40
ITEM | PART NUMBER | TITLE | MATERIAL | DESCRIPTION | QTY

302 Old Castle Brewery
6 Beach Road
Woodstock, 7925
Cape Town

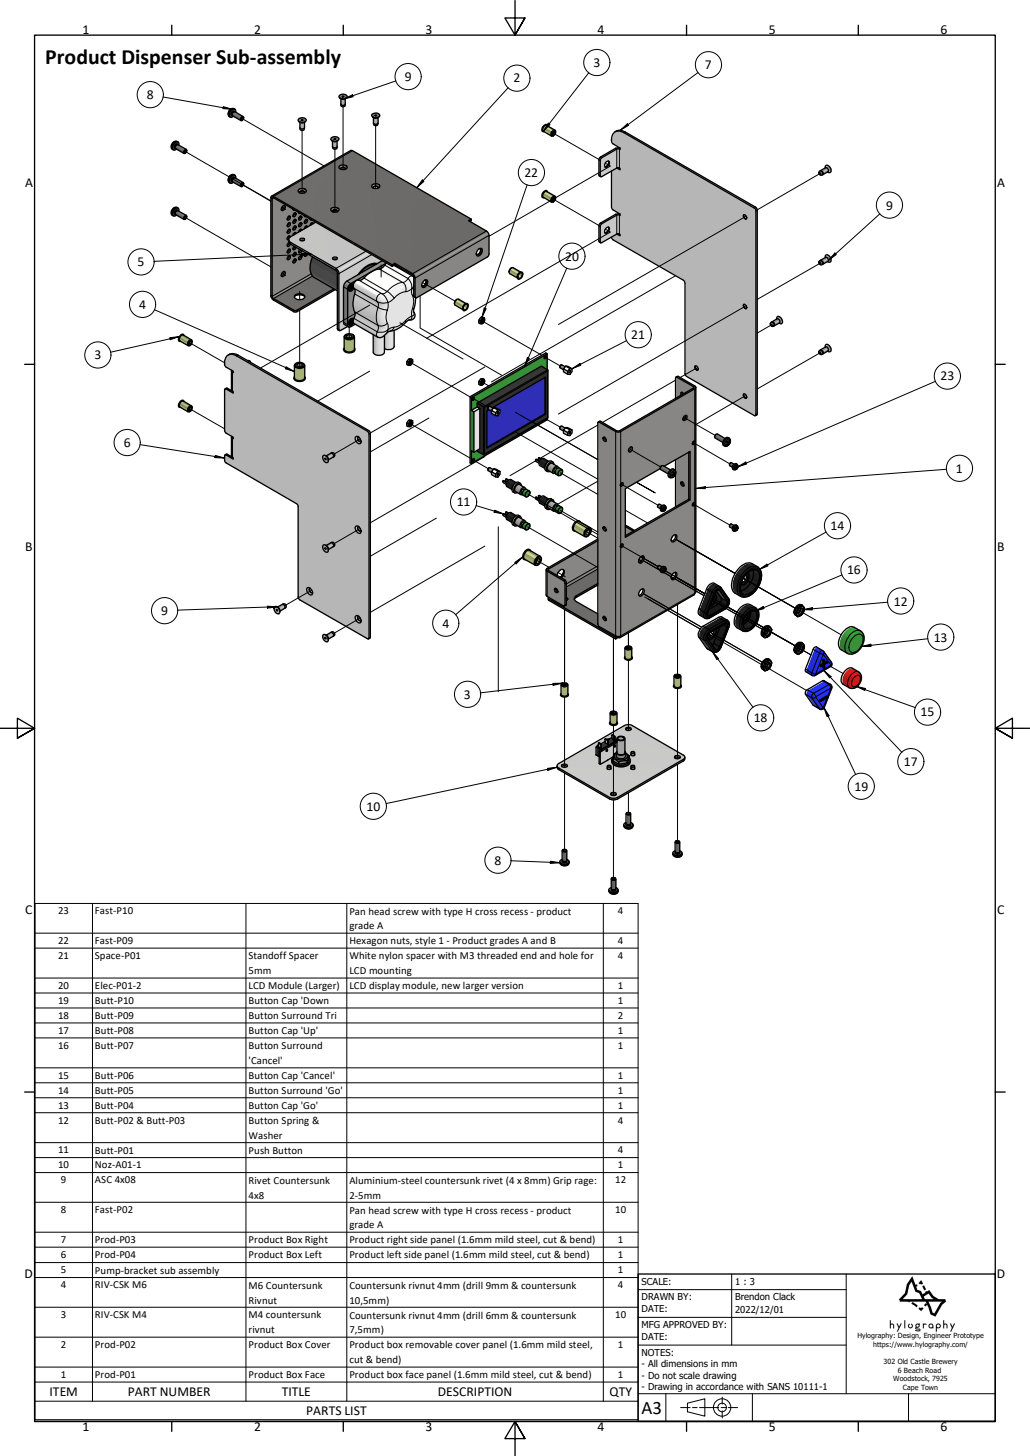
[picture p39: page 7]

Product Dispenser Sub-assembly

23 | Fast-P10 | | Pan head screw with type H cross recess - product grade A | 4

22 | Fast-P09 | | Hexagon nuts, style 1 - Product grades A and B | 4
21 | Space-P01 | Standoff Spacer 5mm | White nylon spacer with M3 threaded end and hole for LCD mounting | 4

20 | Elec-P01-2 | LCD Module (Larger) | LCD display module, new larger version | 1
19 | Butt-P10 | Button Cap 'Down | | 1
18 | Butt-P09 | Button Surround Tri | | 2
17 | Butt-P08 | Button Cap 'Up' | | 1
16 | Butt-P07 | Button Surround 'Cancel' | | 1

15 | Butt-P06 | Button Cap 'Cancel' | | 1
14 | Butt-P05 | Button Surround 'Go' | | 1
13 | Butt-P04 | Button Cap 'Go' | | 1
12 | Butt-P02 & Butt-P03 | Button Spring & Washer | | 4

11 | Butt-P01 | Push Button | | 4
10 | Noz-A01-1 | | | 1
9 | ASC 4x08 | Rivet Countersunk 4x8 | Aluminium-steel countersunk rivet (4 x 8mm) Grip rage: 2-5mm | 12

8 | Fast-P02 | | Pan head screw with type H cross recess - product grade A | 10

7 | Prod-P03 | Product Box Right | Product right side panel (1.6mm mild steel, cut & bend) | 1
6 | Prod-P04 | Product Box Left | Product left side panel (1.6mm mild steel, cut & bend) | 1
5 | Pump-bracket sub assembly | | | 1
4 | RIV-CSK M6 | M6 Countersunk Rivnut | Countersunk rivnut 4mm (drill 9mm & countersunk 10,5mm) | 4

SCALE: | 1 : 3
DRAWN BY: DATE: | Brendon Clack 2022/12/01

3 | RIV-CSK M4 | M4 countersunk rivnut | Countersunk rivnut 4mm (drill 6mm & countersunk 7,5mm) | 10

MFG APPROVED BY:

2 | Prod-P02 | Product Box Cover | Product box removable cover panel (1.6mm mild steel, cut & bend) | 1

1 | Prod-P01 | Product Box Face | Product box face panel (1.6mm mild steel, cut & bend) | 1
ITEM | PART NUMBER | TITLE | DESCRIPTION | QTY

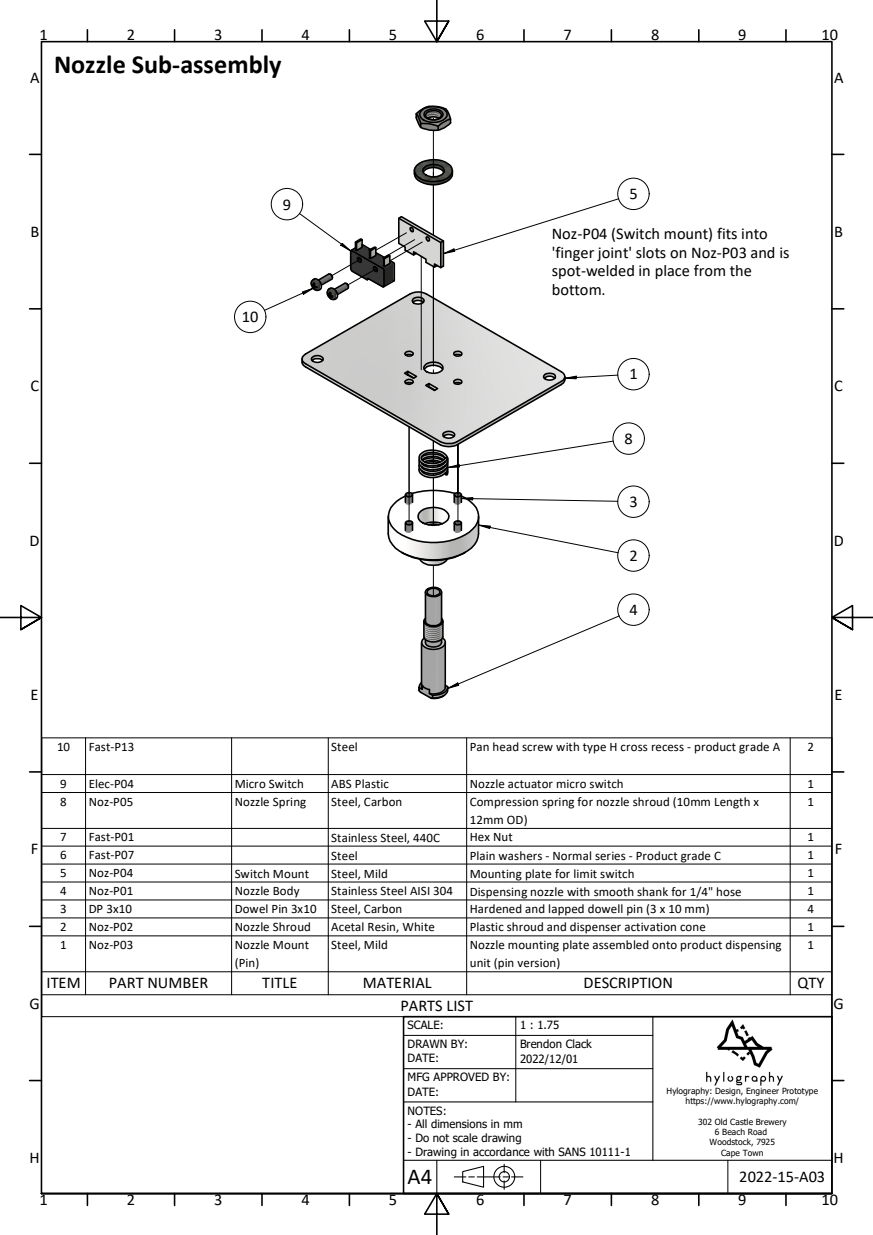
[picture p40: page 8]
PARTS LIST

Nozzle Sub-assembly

Noz-P04 (Switch mount) fits into
'finger joint' slots on Noz-P03 and is
spot-welded in place from the
bottom.

10 | Fast-P13 | | Steel | Pan head screw with type H cross recess - product grade A | 2

9 | Elec-P04 | Micro Switch | ABS Plastic | Nozzle actuator micro switch | 1
8 | Noz-P05 | Nozzle Spring | Steel, Carbon | Compression spring for nozzle shroud (10mm Length x 12mm OD) | 1

7 | Fast-P01 | | Stainless Steel, 440C | Hex Nut | 1
6 | Fast-P07 | | Steel | Plain washers - Normal series - Product grade C | 1
5 | Noz-P04 | Switch Mount | Steel, Mild | Mounting plate for limit switch | 1
4 | Noz-P01 | Nozzle Body | Stainless Steel AISI 304 | Dispensing nozzle with smooth shank for 1/4" hose | 1
3 | DP 3x10 | Dowel Pin 3x10 | Steel, Carbon | Hardened and lapped dowell pin (3 x 10 mm) | 4
2 | Noz-P02 | Nozzle Shroud | Acetal Resin, White | Plastic shroud and dispenser activation cone | 1
1 | Noz-P03 | Nozzle Mount (Pin) | Steel, Mild | Nozzle mounting plate assembled onto product dispensing unit (pin version) | 1

ITEM | PART NUMBER | TITLE | MATERIAL | DESCRIPTION | QTY

SCALE: | 1 : 1.75 | Hylography: Design, Engineer Prototype https://www.hylography.com/302 Old Castle Brewery
DRAWN BY: DATE: | Brendon Clack 2022/12/01

MFG APPROVED BY: DATE:

NOTES:
- All dimensions in mm

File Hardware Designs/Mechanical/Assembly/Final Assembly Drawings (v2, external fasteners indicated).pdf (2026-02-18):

A | A

6

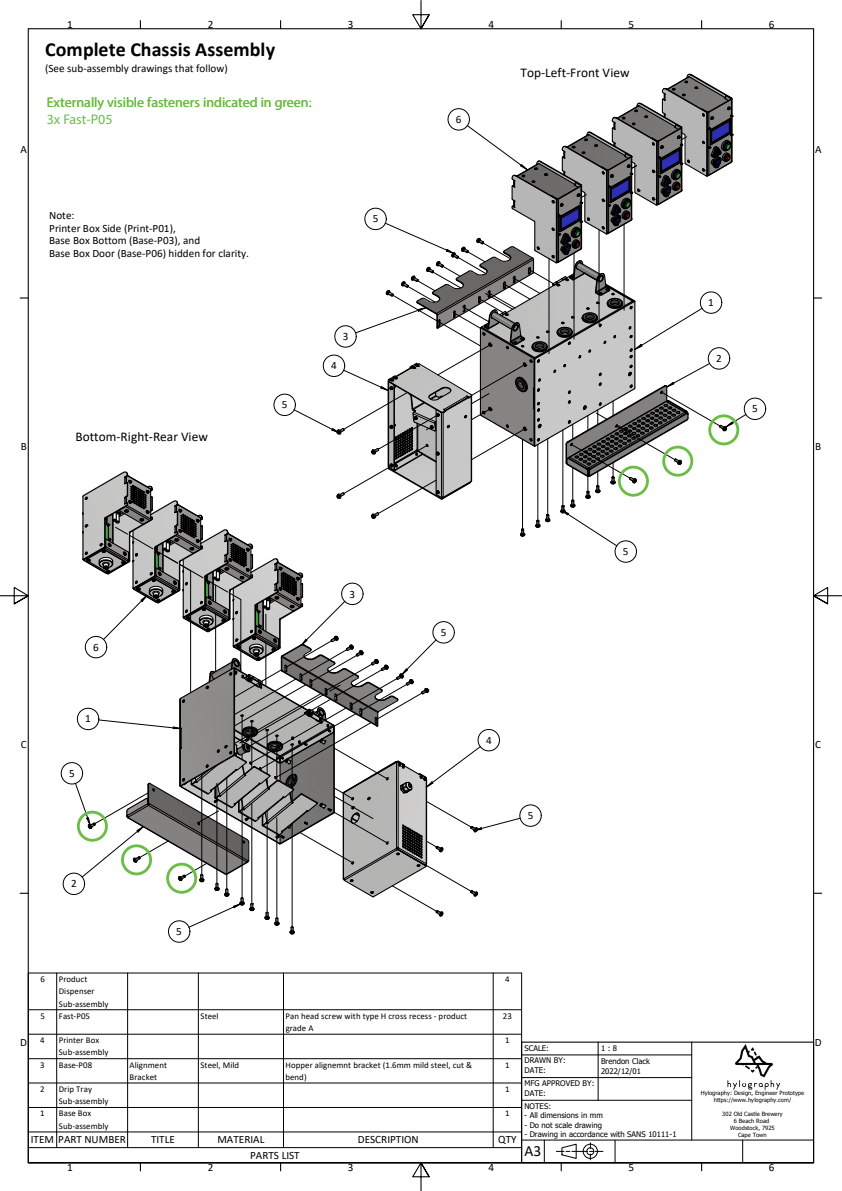
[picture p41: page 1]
Product; Dispenser Sub-assembly; Pan head screw with type H cross recess - product; grade A; 5 Fast-P05; Steel; Printer Box; Sub-assembly; Hopper alignemnt bracket (1.6mm mild steel, cut &; bend); Alignment; Steel, Mild; Bracket; 3 Base-P08; Drip Tray; Base Box; PARTS LIST; ITEM PART NUMBER; TITLE; MATERIAL; DESCRIPTION; QTY; Brendon Clack; DATE:

Complete Chassis Assembly
(See sub-assembly drawings that follow)

Top-Left-Front View

Externally visible fasteners indicated in green. Externally visible fasteners indicated in green:
3x Fast-P05

Note:
Printer Box Side (Print-P01),
Base Box Bottom (Base-P03), and
Base Box Door (Base-P06) hidden for clarity.

Bottom-Right-Rear View

SCALE:
DRAWN BY:
MFG APPROVED BY:
DATE:
NOTES:
- All dimensions in mm
- Do not scale drawing
- Drawing in accordance with SANS 10111-1

Hylography: Design, Engineer Prototype
https://www.hylography.com/
302 Old Castle Brewery
6 Beach Road
Woodstock, 7925
Cape Town

A | A
B | B

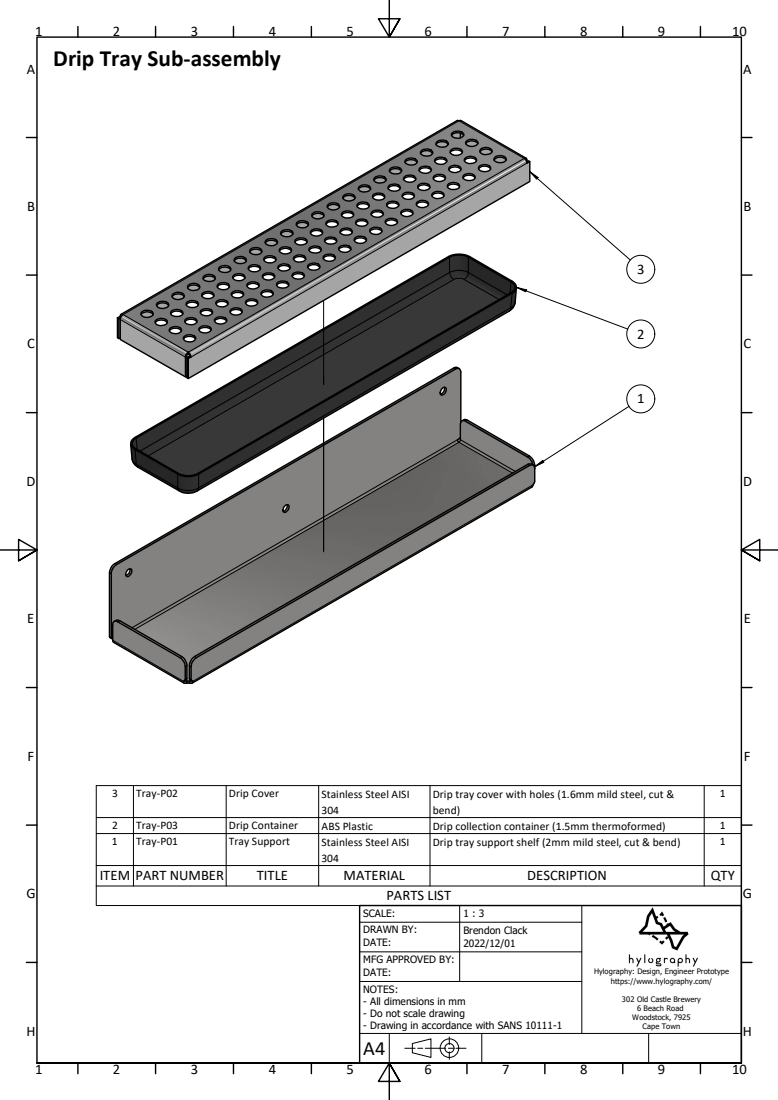
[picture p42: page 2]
Stainless Steel AISI; Drip tray support shelf (2mm mild steel, cut & bend); Tray-P01; Tray Support; ITEM PART NUMBER; TITLE; MATERIAL; DESCRIPTION; QTY; Brendon Clack; DATE:

Drip Tray Sub-assembly

3 | Tray-P02 | Drip Cover | Stainless Steel AISI 304 | Drip tray cover with holes (1.6mm mild steel, cut & bend) | 1

2 | Tray-P03 | Drip Container | ABS Plastic | Drip collection container (1.5mm thermoformed) | 1

PARTS LIST
SCALE:
DRAWN BY:
MFG APPROVED BY:
DATE:
NOTES:
- All dimensions in mm

Hylography: Design, Engineer Prototype
https://www.hylography.com/
302 Old Castle Brewery

A | A

10

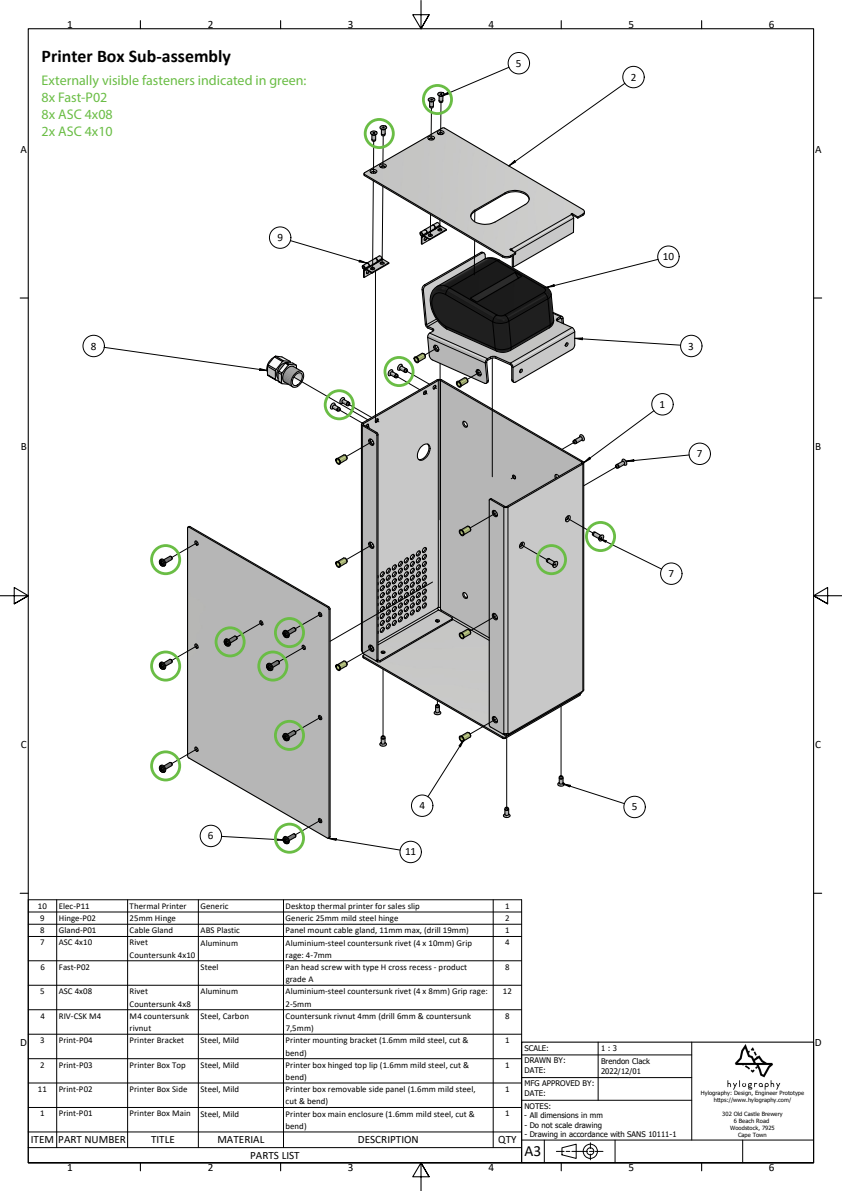
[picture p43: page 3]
Elec-P11; Thermal Printer; Generic; Desktop thermal printer for sales slip; Hinge-P02; 25mm Hinge; Generic 25mm mild steel hinge; Gland-P01; Cable Gland; ABS Plastic; Panel mount cable gland, 11mm max, (drill 19mm); Aluminium-steel countersunk rivet (4 x 10mm) Grip; rage: 4-7mm; Rivet; Aluminum; Countersunk 4x10; ASC 4x10; Pan head screw with type H cross recess - product; grade A; Fast-P02; Steel; Aluminium-steel countersunk rivet (4 x 8mm) Grip rage:; Countersunk 4x8; ASC 4x08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

Printer Box Sub-assembly
Externally visible fasteners indicated in green:
8x Fast-P02
8x ASC 4x08
2x ASC 4x10

SCALE:
DRAWN BY:
MFG APPROVED BY:

A | A

13

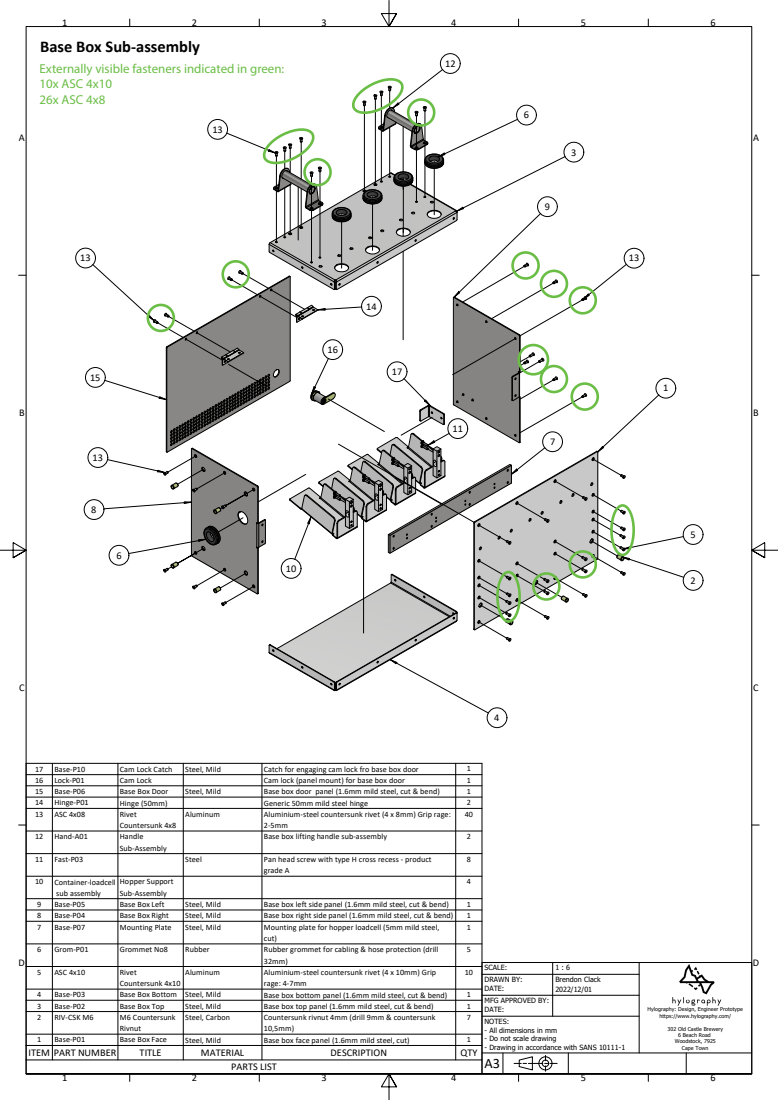
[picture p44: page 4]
Base-P10; Cam Lock Catch; Steel, Mild; Catch for engaging cam lock fro base box door; Lock-P01; Cam Lock; Cam lock (panel mount) for base box door; Base-P06; Base Box Door; Base box door panel (1.6mm mild steel, cut & bend); Hinge-P01; Hinge (50mm); Generic 50mm mild steel hinge; Aluminium-steel countersunk rivet (4 x 8mm) Grip rage:; Rivet; Aluminum; Countersunk 4x8; ASC 4x08; Handle; Base box lifting handle sub-assembly; Sub-Assembly; Hand-A01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

Base Box Sub-assembly
Externally visible fasteners indicated in green:
10x ASC 4x10
26x ASC 4x8

SCALE:
DRAWN BY:
MFG APPROVED BY:

1

3

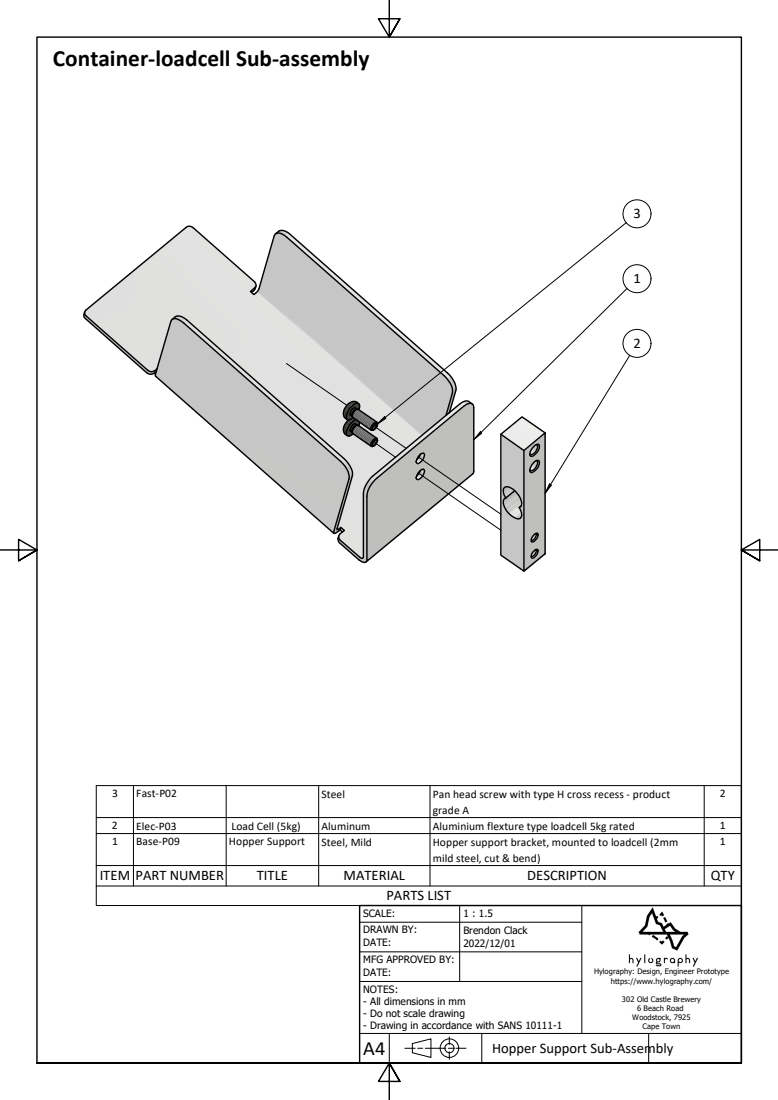
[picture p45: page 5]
Hopper support bracket, mounted to loadcell (2mm; Base-P09; Hopper Support; Steel, Mild; ITEM PART NUMBER; TITLE; MATERIAL; DESCRIPTION; QTY; Brendon Clack; DATE:

Container-loadcell Sub-assembly

3 | Fast-P02 | | Steel | Pan head screw with type H cross recess - product grade A | 2

2 | Elec-P03 | Load Cell (5kg) | Aluminum | Aluminium flexture type loadcell 5kg rated | 1

mild steel, cut & bend)

PARTS LIST

SCALE:
DRAWN BY:
MFG APPROVED BY:
DATE:
NOTES:
- All dimensions in mm

Hylography: Design, Engineer Prototype
https://www.hylography.com/
302 Old Castle Brewery

Hopper Support Sub-Assembly

A | A
B | B

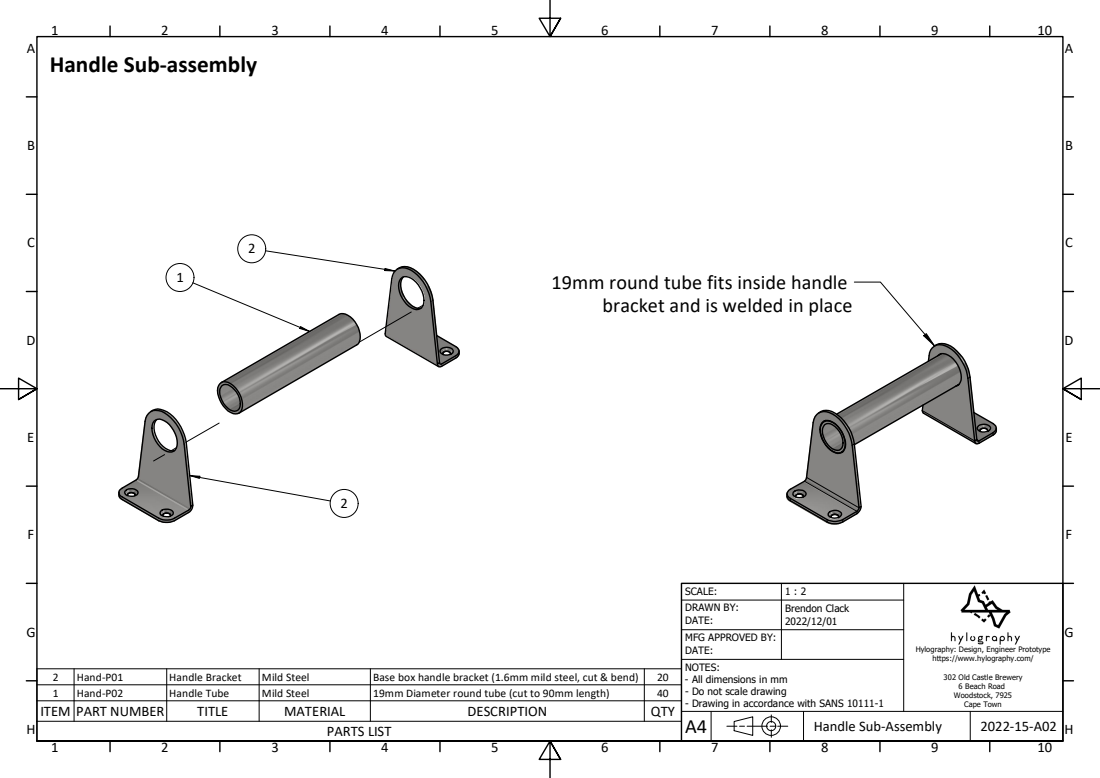
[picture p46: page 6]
Hand-P01; Handle Bracket; Mild Steel; Base box handle bracket (1.6mm mild steel, cut & bend); Hand-P02; Handle Tube; 19mm Diameter round tube (cut to 90mm length); ITEM PART NUMBER; TITLE; MATERIAL; DESCRIPTION; QTY; Brendon Clack; DATE:; Handle Sub-Assembly

Handle Sub-assembly

19mm round tube fits inside handle
bracket and is welded in place

SCALE:
DRAWN BY:
MFG APPROVED BY:
DATE:
NOTES:
- All dimensions in mm
- Do not scale drawing
- Drawing in accordance with SANS 10111-1

Hylography: Design, Engineer Prototype
https://www.hylography.com/
302 Old Castle Brewery
6 Beach Road
Woodstock, 7925
Cape Town

A | A

3

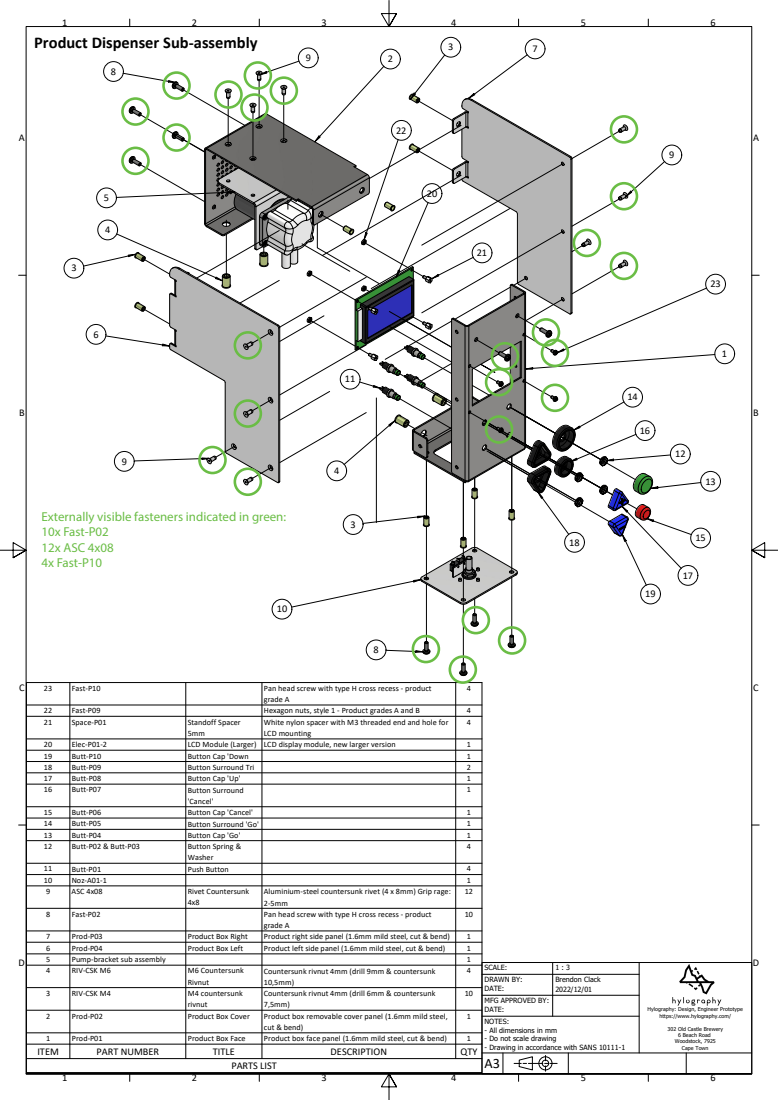
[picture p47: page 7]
Pan head screw with type H cross recess - product; grade A; Fast-P10; Fast-P09; Hexagon nuts, style 1 - Product grades A and B; White nylon spacer with M3 threaded end and hole for; LCD mounting; Standoff Spacer 5mm; Space-P01; Elec-P01-2; LCD Module (Larger); LCD display module, new larger version; Butt-P10; Button Cap 'Down; Butt-P09; Button Surround Tri; Butt-P08; Button Cap 'Up'; Button Surround; 'Cancel'; Butt-P07; Butt-P06; Button Cap 'Cancel'; Butt-P05; Button Surround 'Go'; Butt-P04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

Product Dispenser Sub-assembly

Externally visible fasteners indicated in green:
10x Fast-P02
12x ASC 4x08
4x Fast-P10

SCALE:
DRAWN BY:
MFG APPROVED BY:

A | A
B | B

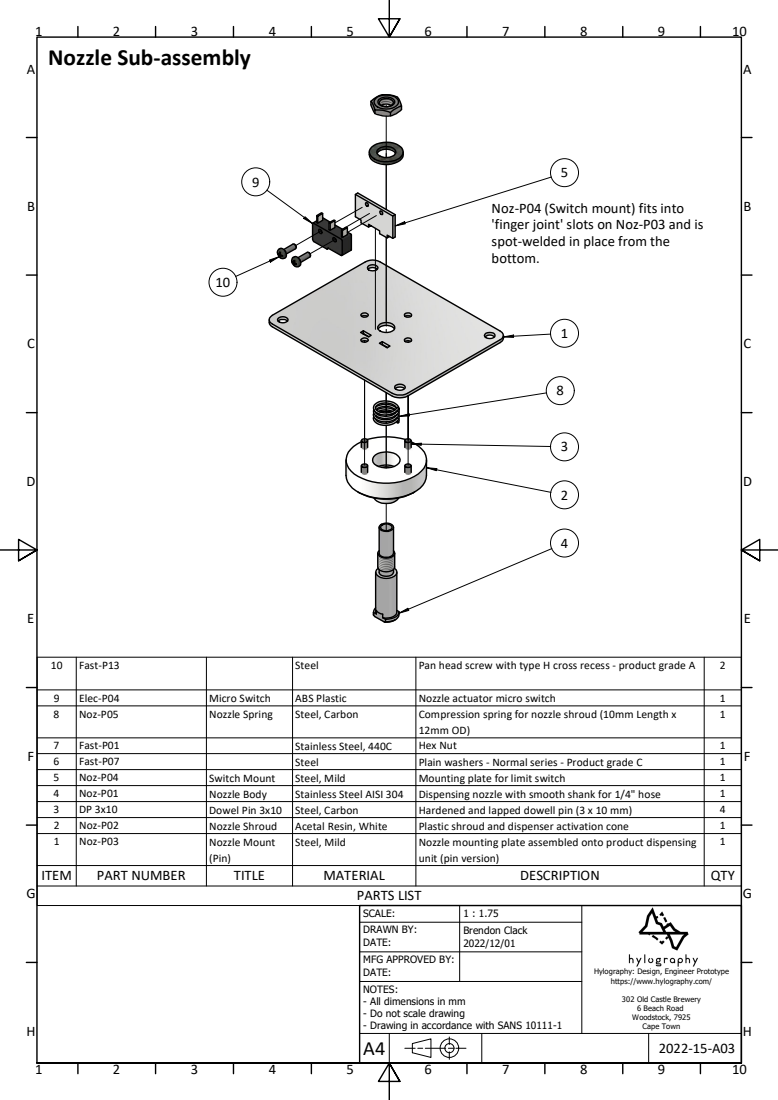
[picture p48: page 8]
Nozzle mounting plate assembled onto product dispensing; Nozzle Mount; Steel, Mild; (Pin); Noz-P03; ITEM; PART NUMBER; TITLE; MATERIAL; DESCRIPTION; QTY; Brendon Clack; DATE:

Nozzle Sub-assembly

Noz-P04 (Switch mount) fits into
'finger joint' slots on Noz-P03 and is
spot-welded in place from the
bottom.

10 | Fast-P13 | | Steel | Pan head screw with type H cross recess - product grade A | 2

9 | Elec-P04 | Micro Switch | ABS Plastic | Nozzle actuator micro switch | 1
8 | Noz-P05 | Nozzle Spring | Steel, Carbon | Compression spring for nozzle shroud (10mm Length x 12mm OD) | 1

7 | Fast-P01 | | Stainless Steel, 440C | Hex Nut | 1
6 | Fast-P07 | | Steel | Plain washers - Normal series - Product grade C | 1
5 | Noz-P04 | Switch Mount | Steel, Mild | Mounting plate for limit switch | 1
4 | Noz-P01 | Nozzle Body | Stainless Steel AISI 304 | Dispensing nozzle with smooth shank for 1/4" hose | 1
3 | DP 3x10 | Dowel Pin 3x10 | Steel, Carbon | Hardened and lapped dowell pin (3 x 10 mm) | 4
2 | Noz-P02 | Nozzle Shroud | Acetal Resin, White | Plastic shroud and dispenser activation cone | 1

unit (pin version)

PARTS LIST

SCALE:
DRAWN BY:
MFG APPROVED BY:
DATE:
NOTES:
- All dimensions in mm

Hylography: Design, Engineer Prototype
https://www.hylography.com/
302 Old Castle Brewery

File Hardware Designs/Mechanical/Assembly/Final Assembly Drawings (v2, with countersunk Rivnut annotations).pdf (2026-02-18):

A | A

6

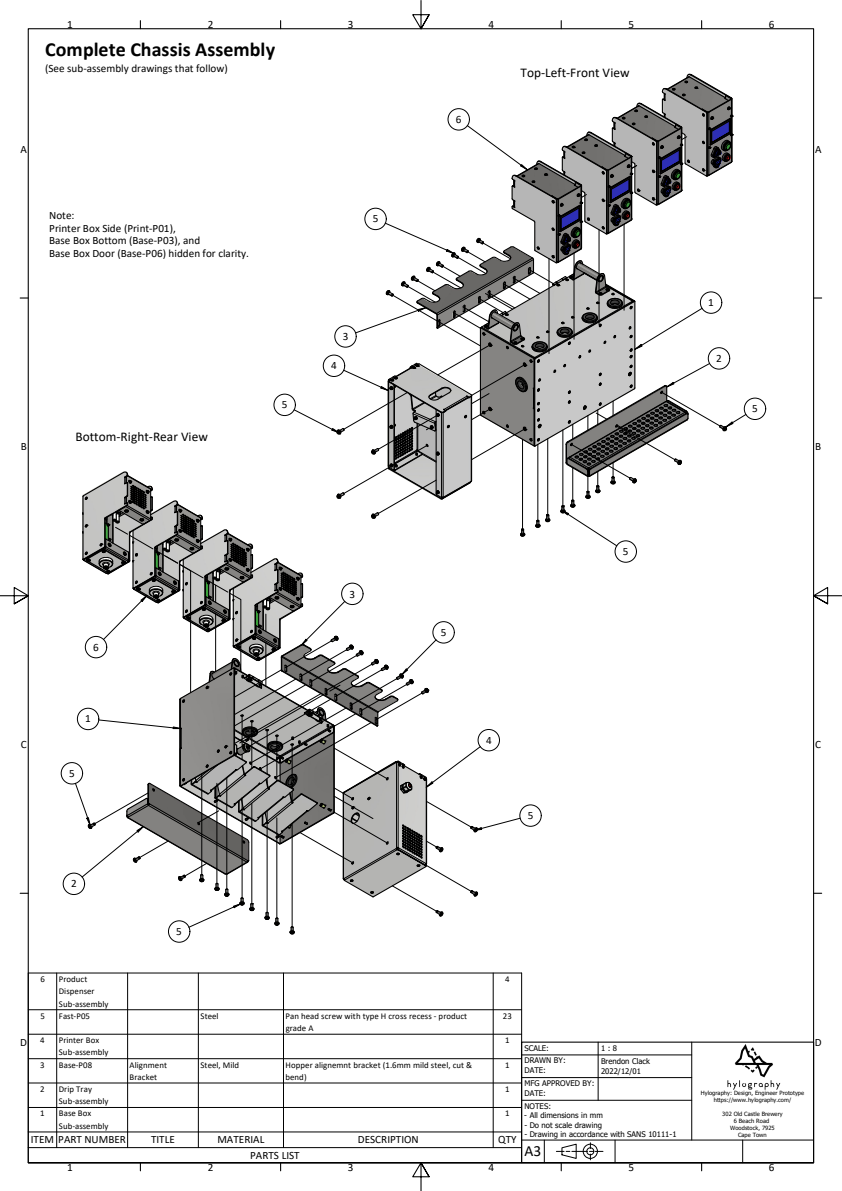
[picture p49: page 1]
Product; Dispenser Sub-assembly; Pan head screw with type H cross recess - product; grade A; 5 Fast-P05; Steel; Printer Box; Sub-assembly; Hopper alignemnt bracket (1.6mm mild steel, cut &; bend); Alignment; Steel, Mild; Bracket; 3 Base-P08; Drip Tray; Base Box; PARTS LIST; ITEM PART NUMBER; TITLE; MATERIAL; DESCRIPTION; QTY; Brendon Clack; DATE:

Complete Chassis Assembly
(See sub-assembly drawings that follow)

Top-Left-Front View

Note:
Printer Box Side (Print-P01),
Base Box Bottom (Base-P03), and
Base Box Door (Base-P06) hidden for clarity.

Bottom-Right-Rear View

SCALE:
DRAWN BY:
MFG APPROVED BY:
DATE:
NOTES:
- All dimensions in mm
- Do not scale drawing
- Drawing in accordance with SANS 10111-1

Hylography: Design, Engineer Prototype
https://www.hylography.com/
302 Old Castle Brewery
6 Beach Road
Woodstock, 7925
Cape Town

A | A
B | B

Stainless Steel AISI; Drip tray support shelf (2mm mild steel, cut & bend); Tray-P01; Tray Support; ITEM PART NUMBER; TITLE; MATERIAL; DESCRIPTION; QTY; Brendon Clack; DATE:

Drip Tray Sub-assembly

3 | Tray-P02 | Drip Cover | Stainless Steel AISI 304 | Drip tray cover with holes (1.6mm mild steel, cut & bend) | 1

2 | Tray-P03 | Drip Container | ABS Plastic | Drip collection container (1.5mm thermoformed) | 1

PARTS LIST
SCALE:
DRAWN BY:
MFG APPROVED BY:
DATE:
NOTES:
- All dimensions in mm

Hylography: Design, Engineer Prototype
https://www.hylography.com/
302 Old Castle Brewery

A | A

10

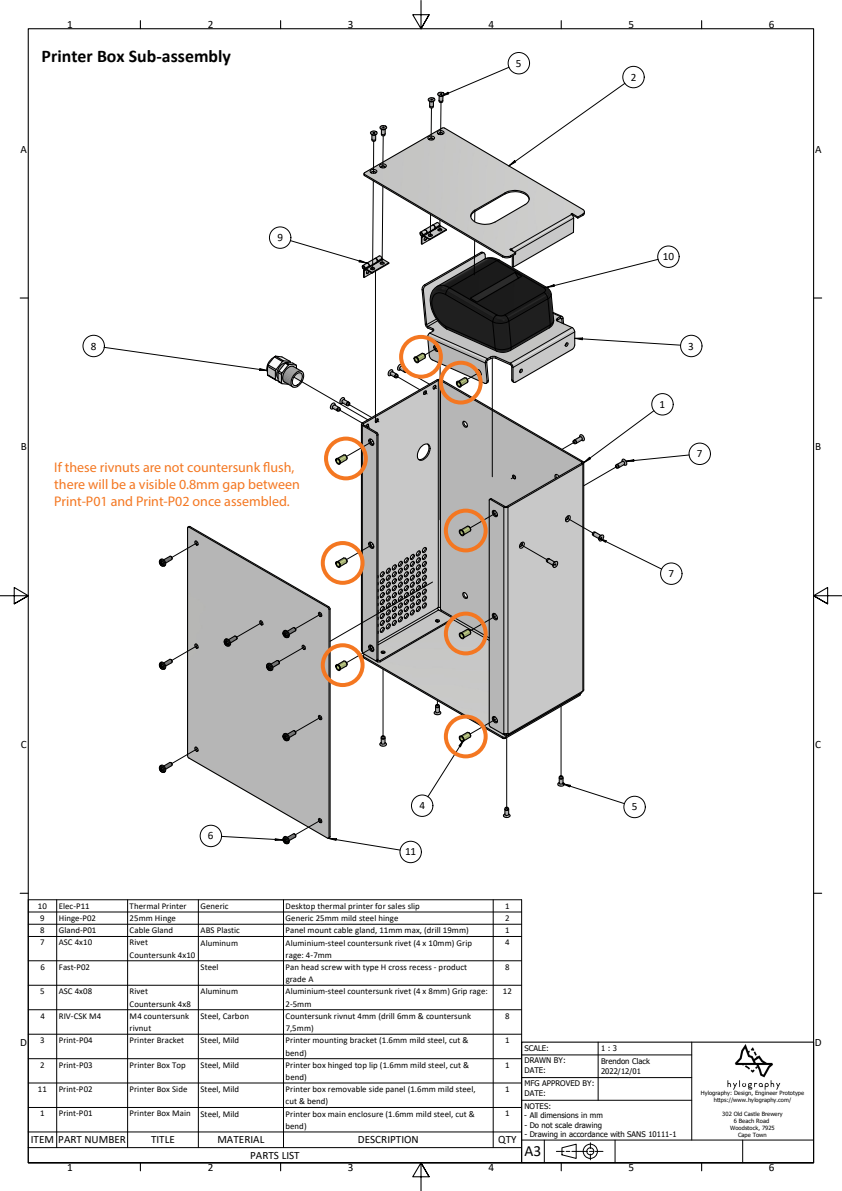
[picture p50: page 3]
Elec-P11; Thermal Printer; Generic; Desktop thermal printer for sales slip; Hinge-P02; 25mm Hinge; Generic 25mm mild steel hinge; Gland-P01; Cable Gland; ABS Plastic; Panel mount cable gland, 11mm max, (drill 19mm); Aluminium-steel countersunk rivet (4 x 10mm) Grip; rage: 4-7mm; Rivet; Aluminum; Countersunk 4x10; ASC 4x10; Pan head screw with type H cross recess - product; grade A; Fast-P02; Steel; Aluminium-steel countersunk rivet (4 x 8mm) Grip rage:; Countersunk 4x8; ASC 4x08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

Printer Box Sub-assembly

If these rivnuts are not countersunk ush,
there will be a visible 0.8mm gap between
Print-P01 and Print-P02 once assembled.

SCALE:
DRAWN BY:
MFG APPROVED BY:

A | A

13

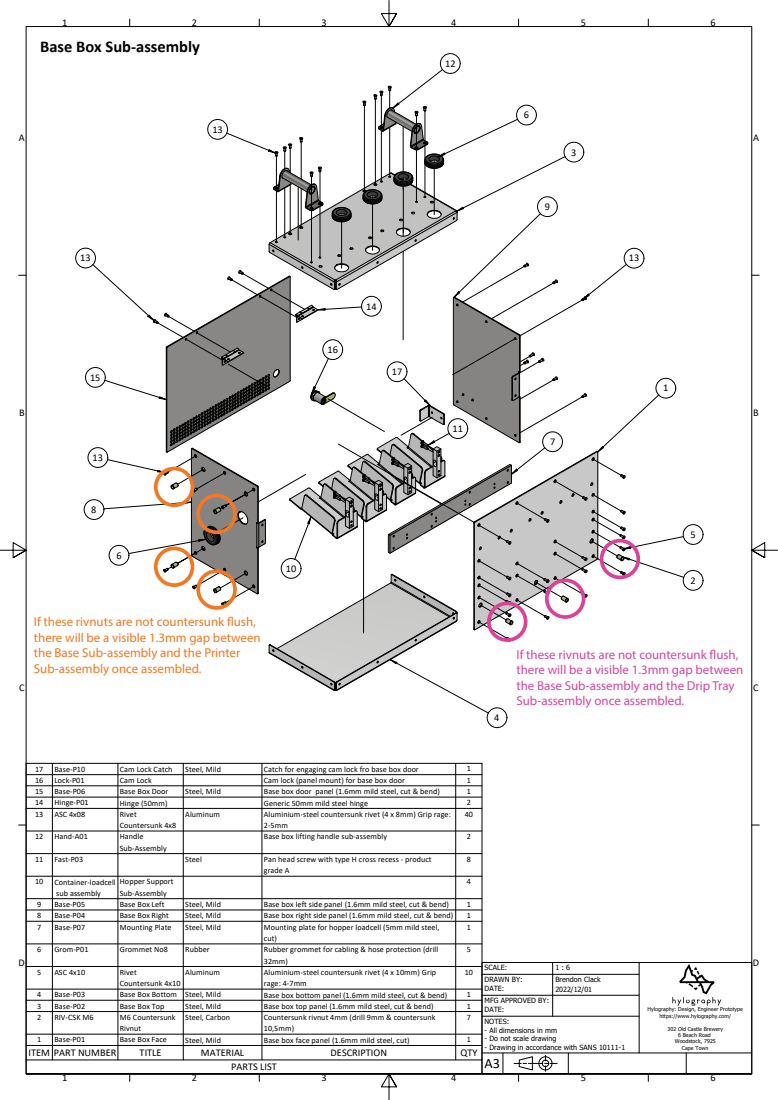
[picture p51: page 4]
Base-P10; Cam Lock Catch; Steel, Mild; Catch for engaging cam lock fro base box door; Lock-P01; Cam Lock; Cam lock (panel mount) for base box door; Base-P06; Base Box Door; Base box door panel (1.6mm mild steel, cut & bend); Hinge-P01; Hinge (50mm); Generic 50mm mild steel hinge; Aluminium-steel countersunk rivet (4 x 8mm) Grip rage:; Rivet; Aluminum; Countersunk 4x8; ASC 4x08; Handle; Base box lifting handle sub-assembly; Sub-Assembly; Hand-A01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

Base Box Sub-assembly

If these rivnuts are not countersunk ush,
there will be a visible 1.3mm gap between
the Base Sub-assembly and the Printer
Sub-assembly once assembled.

the Base Sub-assembly and the Drip Tray

SCALE:
DRAWN BY:
MFG APPROVED BY:

1

3

Hopper support bracket, mounted to loadcell (2mm; Base-P09; Hopper Support; Steel, Mild; ITEM PART NUMBER; TITLE; MATERIAL; DESCRIPTION; QTY; Brendon Clack; DATE:

Container-loadcell Sub-assembly

3 | Fast-P02 | | Steel | Pan head screw with type H cross recess - product grade A | 2

2 | Elec-P03 | Load Cell (5kg) | Aluminum | Aluminium flexture type loadcell 5kg rated | 1

mild steel, cut & bend)

PARTS LIST

SCALE:
DRAWN BY:
MFG APPROVED BY:
DATE:
NOTES:
- All dimensions in mm

Hylography: Design, Engineer Prototype
https://www.hylography.com/
302 Old Castle Brewery

Hopper Support Sub-Assembly

A | A
B | B

Hand-P01; Handle Bracket; Mild Steel; Base box handle bracket (1.6mm mild steel, cut & bend); Hand-P02; Handle Tube; 19mm Diameter round tube (cut to 90mm length); ITEM PART NUMBER; TITLE; MATERIAL; DESCRIPTION; QTY; Brendon Clack; DATE:; Handle Sub-Assembly

Handle Sub-assembly

19mm round tube fits inside handle
bracket and is welded in place

SCALE:
DRAWN BY:
MFG APPROVED BY:
DATE:
NOTES:
- All dimensions in mm
- Do not scale drawing
- Drawing in accordance with SANS 10111-1

Hylography: Design, Engineer Prototype
https://www.hylography.com/
302 Old Castle Brewery
6 Beach Road
Woodstock, 7925
Cape Town

A | A

3

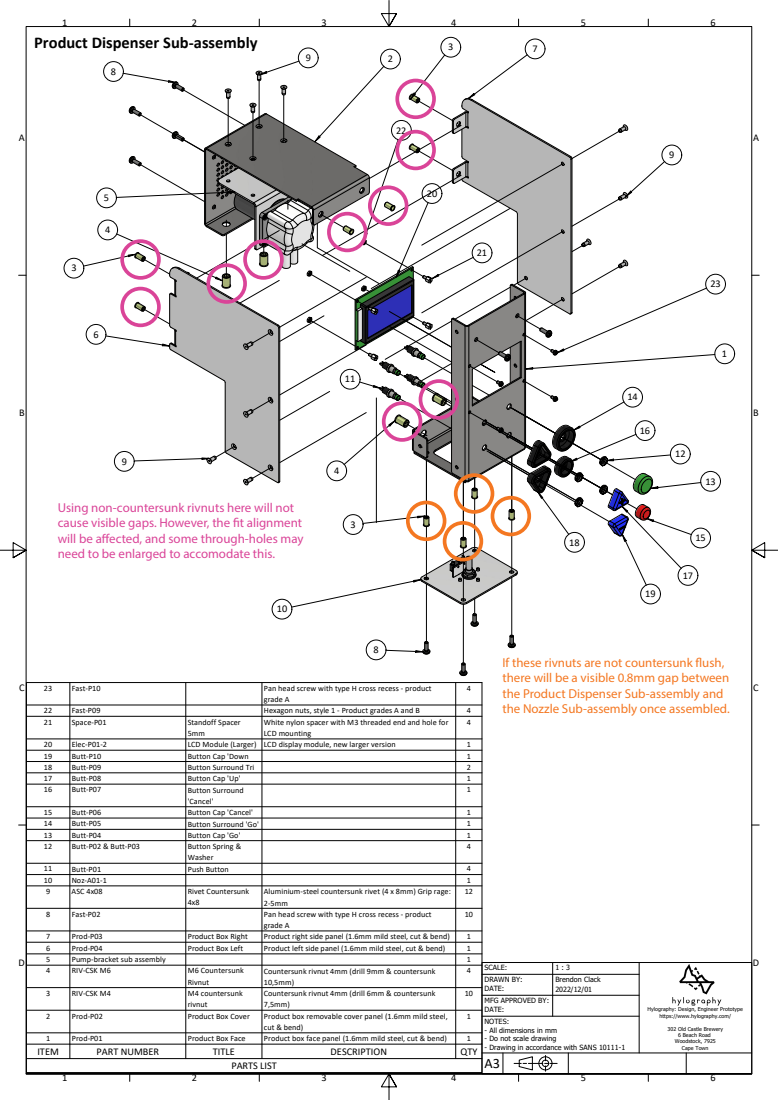
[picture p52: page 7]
Pan head screw with type H cross recess - product; grade A; Fast-P10; Fast-P09; Hexagon nuts, style 1 - Product grades A and B; White nylon spacer with M3 threaded end and hole for; LCD mounting; Standoff Spacer 5mm; Space-P01; Elec-P01-2; LCD Module (Larger); LCD display module, new larger version; Butt-P10; Button Cap 'Down; Butt-P09; Button Surround Tri; Butt-P08; Button Cap 'Up'; Button Surround; 'Cancel'; Butt-P07; Butt-P06; Button Cap 'Cancel'; Butt-P05; Button Surround 'Go'; Butt-P04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

Product Dispenser Sub-assembly

Using non-countersunk rivnuts here will not
cause visible gaps. However, the t alignment
will be aected, and some through-holes may
need to be enlarged to accomodate this.

If these rivnuts are not countersunk ush,
there will be a visible 0.8mm gap between
the Product Dispenser Sub-assembly and
the Nozzle Sub-assembly once assembled.

SCALE:
DRAWN BY:
MFG APPROVED BY:

A | A
B | B

Nozzle mounting plate assembled onto product dispensing; Nozzle Mount; Steel, Mild; (Pin); Noz-P03; ITEM; PART NUMBER; TITLE; MATERIAL; DESCRIPTION; QTY; Brendon Clack; DATE:

Nozzle Sub-assembly

Noz-P04 (Switch mount) fits into
'finger joint' slots on Noz-P03 and is
spot-welded in place from the
bottom.

10 | Fast-P13 | | Steel | Pan head screw with type H cross recess - product grade A | 2

9 | Elec-P04 | Micro Switch | ABS Plastic | Nozzle actuator micro switch | 1
8 | Noz-P05 | Nozzle Spring | Steel, Carbon | Compression spring for nozzle shroud (10mm Length x 12mm OD) | 1

7 | Fast-P01 | | Stainless Steel, 440C | Hex Nut | 1
6 | Fast-P07 | | Steel | Plain washers - Normal series - Product grade C | 1
5 | Noz-P04 | Switch Mount | Steel, Mild | Mounting plate for limit switch | 1
4 | Noz-P01 | Nozzle Body | Stainless Steel AISI 304 | Dispensing nozzle with smooth shank for 1/4" hose | 1
3 | DP 3x10 | Dowel Pin 3x10 | Steel, Carbon | Hardened and lapped dowell pin (3 x 10 mm) | 4
2 | Noz-P02 | Nozzle Shroud | Acetal Resin, White | Plastic shroud and dispenser activation cone | 1

unit (pin version)

PARTS LIST

SCALE:
DRAWN BY:
MFG APPROVED BY:
DATE:
NOTES:
- All dimensions in mm

Hylography: Design, Engineer Prototype
https://www.hylography.com/
302 Old Castle Brewery

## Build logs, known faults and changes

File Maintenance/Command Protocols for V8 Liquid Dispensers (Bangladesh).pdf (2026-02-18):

## Command Protocol

2024/12/03

Hardware: Main ESP Board (called Buttons or Motor ESP) Firmware: >= v3.4.0 (buttonfunctionpiov3)
BAUD rate: 115200

Command Protocol
End-of-line delimiter: new-line character \n
Argument delimiter: comma character ,
Structure: | COMMAND-NUMBER <, comma separated arguments>\n

Example Commands (excluding quote characters)
Set flowrates for dispenser 1 to 4 to 1.2 ml/s, 2.3 ml/s, 1.4 ml/s and 2.5 ml/s “20,1.2,2.3,1.4,2.5\n”

Set the volume-price table for Dispenser 1 to 50 ml: 100 TK
100 ml: 200 TK
250 ml: 500 TK
“23,1,50,100,100,200,250,500\n”
Name | # Description | Arguments
DX_ID | 0 | Print machine ID and
firmware number
CFG_FLOW_RATE | 20 | Set flowrate in ml/s per
dispenser

flowrate_1, flowrate_2, flowrate_3, flowrate_4
CFG_PRODUCT_TABLE | 23 | Set price table (volume
and price) for a
dispenser (product)

Dispenser number,
volume_1 (ml), price_1 (tk), volume_2 (ml), price_2 (tk), volume_3 (ml), price_3 (tk)

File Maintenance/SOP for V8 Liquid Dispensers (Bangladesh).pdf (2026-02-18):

# STANDARD OPERATING PROCEDURE:

## OPERATION OF SOAP/SHAMPOO DISPENSING MACHINE

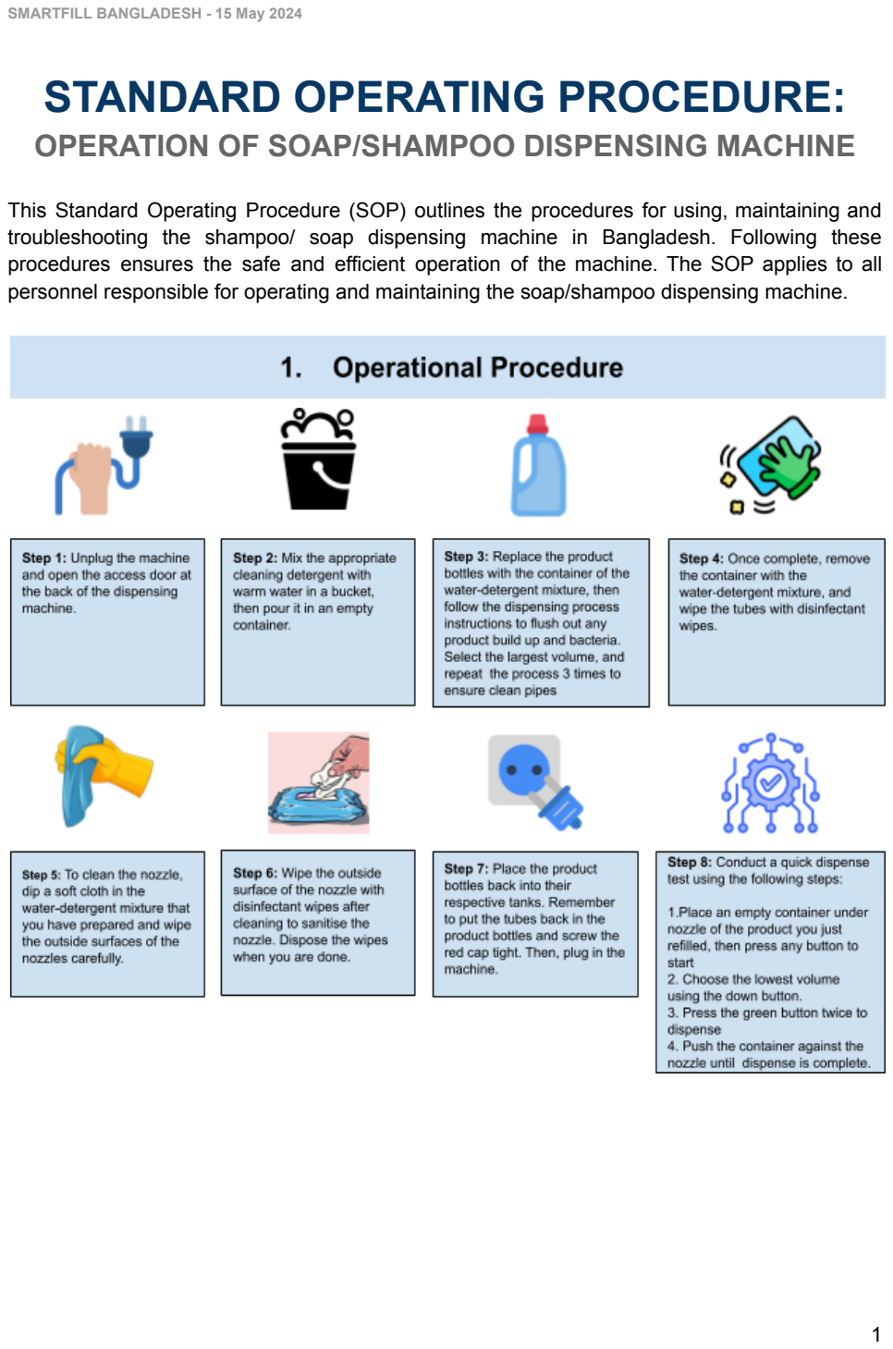
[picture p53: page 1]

SMARTFILL BANGLADESH - 15 May 2024

This Standard Operating Procedure (SOP) outlines the procedures for using, maintaining and troubleshooting the shampoo/ soap dispensing machine in Bangladesh. Following these procedures ensures the safe and efficient operation of the machine. The SOP applies to all personnel responsible for operating and maintaining the soap/shampoo dispensing machine.

### 1.1 Pre- Operational Check

The following should be done at the beginning of the day. Should any issues arise during the pre-operational check, please refer to the troubleshooting guide on page 5.

Pre-Operational Activity | Pre-Operational Activity Examples
1. Check if the dispensing machine plug is plugged into the electrical socket and is working. | - Check if the electrical socket on the wall is switched on.
2. Check if all screens are on and showing text. | - Check if all the screens turn blue and text displays when you turn on the machine. - Check if the instructions show on the screen.
3. Check for any product leaks underneath the nozzles and around the dispensing machine. | - Check if there are more product drips on the drip tray than usual. If there is, please open the back access door and check the valves for damage, or looseness. Should the pipes and/or bottle caps be loose, please tighten the loose connections. If damaged or worn out, please contact the manufacturer (page 6) for replacements. - Check if there is any product leaking from the machine itself.
4. Check for any visible damage to the dispensing machine | - Check if there are any cracks on the nozzles. - Check if there is any dried soap or shampoo on the nozzle that might prevent it from dispensing properly. If there is, use a damp cloth and wipe off any dried soap/shampoo on the nozzle. - Check if there are any exposed wires on the plug.
5. Check if all the buttons are working | - Check if the buttons stick when pressed. If they do, wipe off any residue around the buttons. - Check if the screen instructions change when using the buttons. - each individually: - GREEN, RED, UP and DOWN

6. Check if the printer is on, connected and has enough printing paper.
- Open the printer flap and check if the printer light is glowing BLUE when the dispensing machine is on. If the printer light is GREEN then restart the dispenser using the main RED on/off switch.
- Check if there is enough printing paper in the printer. If the printing paper seems low and might not be enough for your daily printing job, please replace it by:
1. Opening the top cover of the printer.

### 2. Carefully removing any remaining low-running

paper from the printing tray.
3.Placing the new printing paper neatly into the tray.
- Please ensure that it is correctly aligned with the printing tray.
4. Close the top cover of the printer securely.

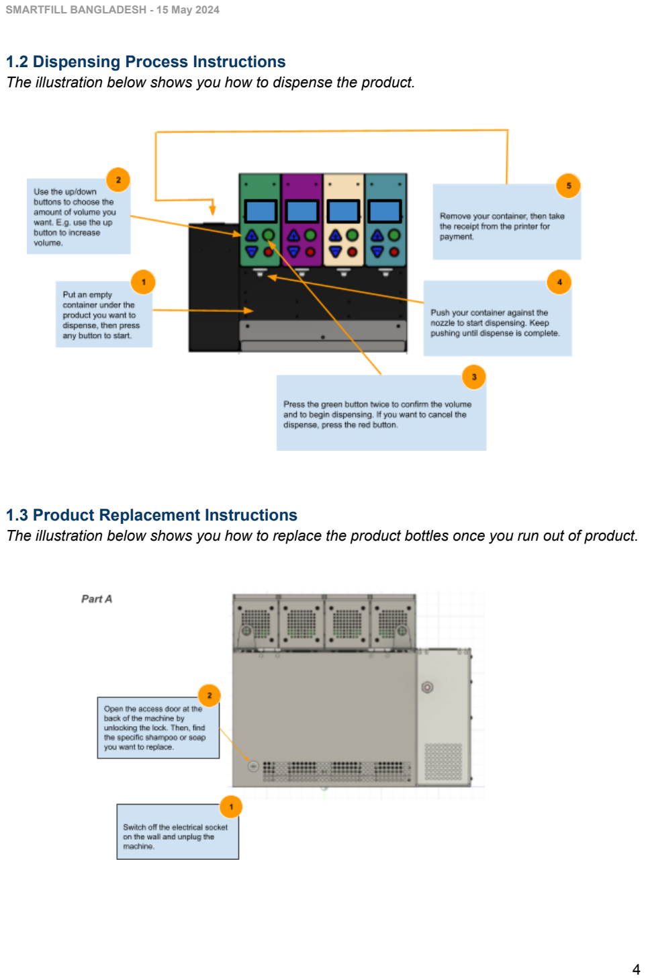
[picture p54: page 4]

### 1.2 Dispensing Process Instructions

The illustration below shows you how to dispense the product.

### 1.3 Product Replacement Instructions

The illustration below shows you how to replace the product bottles once you run out of product.

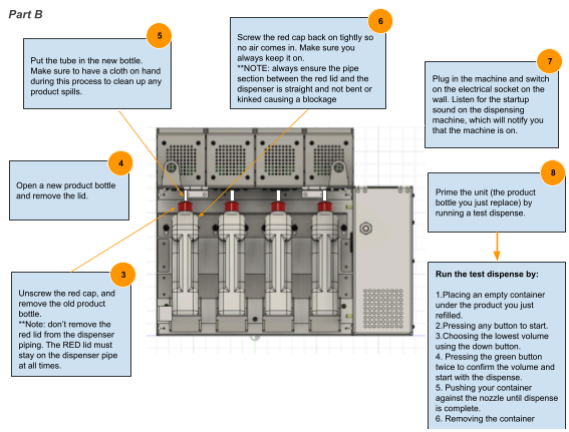
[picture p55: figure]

### 2.1 Basic Cleaning and Maintenance:

1. Do a dry wipe of the dispenser body once a week. You can do this by taking a microfiber cloth and wiping down the exterior surfaces of the machine including the nozzles, buttons, screens, the top and sides of the machine, etc. Please do not put any soap or water on the cloth.
2. In the morning and afternoon, use disinfectant wipes to wipe off any product spills in the drip tray and underneath the nozzle.
3. Wipe any spills or product leakage during bottle replacement to avoid product build up.
4. Do deep cleaning of tubes and nozzles once a month. Read the instructions below.

### 2.2 Deep Cleaning Instructions:

The following steps guide you on how to deep clean the tubes and nozzles of the dispensing machine.

### 2.3 Quality Control Measures:

1. Do a quick dispense test, after every product replacement to prime the unit (product bottle). Should there be any issues that arise during the dispense test, write them down and follow the troubleshooting guide on page 5.
2. Regularly check the product level of bottles and ensure there are enough in store to replace as needed when empty.
3. Keep a record of the cleaning schedule.

### Troubleshooting:

Should the dispensing machine stop working try to identify the following issue/s:

Issues you may encounter | Possible Solution
No power/screens not turning on/no printer light | - Check if the dispensing machine is plugged into the electrical socket on the wall and that the power is on. - If there is no power at the socket the battery may be running low, please wait until the power returns. - Switch off the dispenser and ensure that there is power at the socket. - Restart the dispensing machine and check again once the mains power has returned.
No response from buttons | - Check if the dispensing machine is plugged into the electrical socket on the wall and that the power is on. - If there is no power at the socket the battery may be running low, please wait until the power returns. - Restart the dispensing machine by switching the red power off and on switch, and check again. - Ensure that the screens are displaying text and the dispenser is powered on properly.
Buttons are triggering incorrect response, e.g. when pressing up button it responds with the down screen | - Restart the dispensing machine by switching the red power off and on switch and check again. - If the problem continues, call support.
No text on screens | - Check if the dispensing machine is plugged into the electrical socket on the wall and that the power is on. - If there is no power at the socket the battery may be running low, please wait until the power returns. - Restart the dispensing machine and check again once the mains power has returned.
Dispense does not start | - Check if the dispensing machine is plugged into the electrical socket on the wall and that the power is on. - If there is no power at the socket the battery may be running low, please wait until the power returns. - Restart the dispensing machine and check again once the mains power has returned.
No product coming out, but motor is turning | - Check product level of the jerry can and replace if necessary. - Check for any kinks in tubing or any clogging in tubing or nozzle and fix kinks and clean out any obstructions.

| - Restart the dispensing machine and check again.
Not enough product dispensed | - Check product level of the jerry can and replace if necessary. - Ensure the tubing reaches the bottom of the jerry can for product to be dispensed. - Check for any kinks in tubing or any clogging in tubing or nozzle and fix kinks and clean out any obstructions. - Restart the dispensing machine and check again.
Not printing invoice/slip | - Check if there is paper in the printer and replace it if necessary. - Check if the printer is on (green light on) and check if the printer is connected to the dispenser (blue light is on). - If the blue light is not on, restart the printer by pressing its power button and then restart the dispensing machine and check for connection again.
Motor turns when a dispense was not triggered (Auto dispense) | - Check if the dispensing machine is plugged into the electrical socket on the wall and that the power is on. - If there is no power at the socket the battery may be running low, please wait until the power returns. - Restart the dispensing machine and check again.

Should the above solutions not work or you encounter more problems, please contact Smartfill. +880 1841-635310.

The issue/problem can be emailed to moon@dydx.digital.

### Safety Precautions:

1. Keep the area spill-free to avoid slips, e.g. regularly wipe off product spills throughout the day.
2. Wear gloves when handling products to maintain sanitation and to avoid any skin irritation.
3. Always make sure that the machine is unplugged before replacing the product bottle or cleaning.
4. If the machine is damaged, e.g. if there are any exposed wires, stop using the machine and report the damages immediately.
5. Provide proper training for everyone operating the machine.

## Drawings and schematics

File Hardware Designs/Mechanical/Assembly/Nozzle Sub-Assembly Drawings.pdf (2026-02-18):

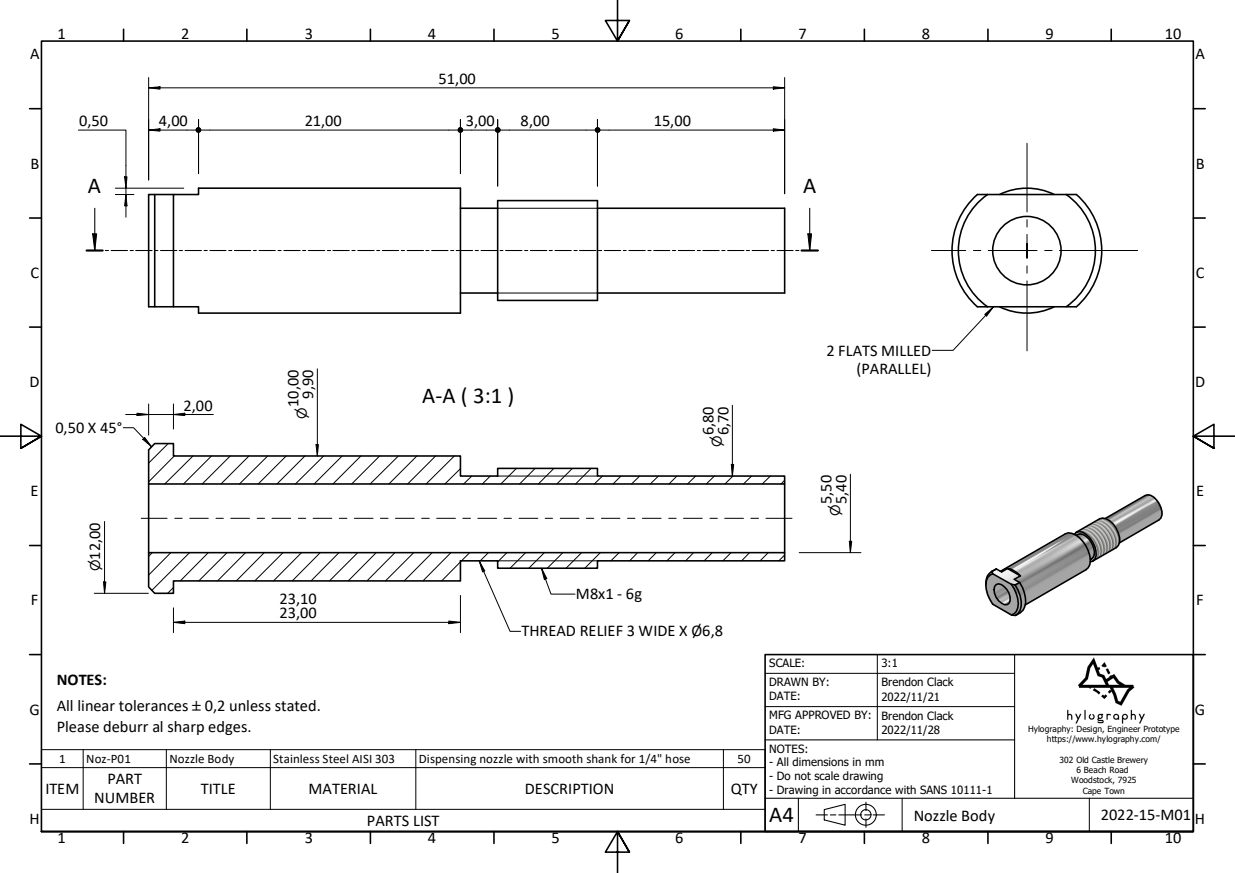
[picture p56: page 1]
PARTS LIST; Nozzle Body; 2 FLATS MILLED

THREAD RELIEF 3 WIDE X Ø6,8

NOTES:
All linear tolerances `0,2 unless stated.
Please deburr al sharp edges.

DRAWN BY: DATE: | Brendon Clack 2022/11/21

MFG APPROVED BY: DATE: | Brendon Clack 2022/11/28

Hylography: Design, Engineer Prototype
https://www.hylography.com/

- All dimensions in mm
- Do not scale drawing
- Drawing in accordance with SANS 10111-1

1 | Noz-P01 | Nozzle Body | Stainless Steel AISI 303 | Dispensing nozzle with smooth shank for 1/4" hose | 50
ITEM | PART NUMBER | TITLE | MATERIAL | DESCRIPTION | QTY

302 Old Castle Brewery
6 Beach Road
Woodstock, 7925
Cape Town

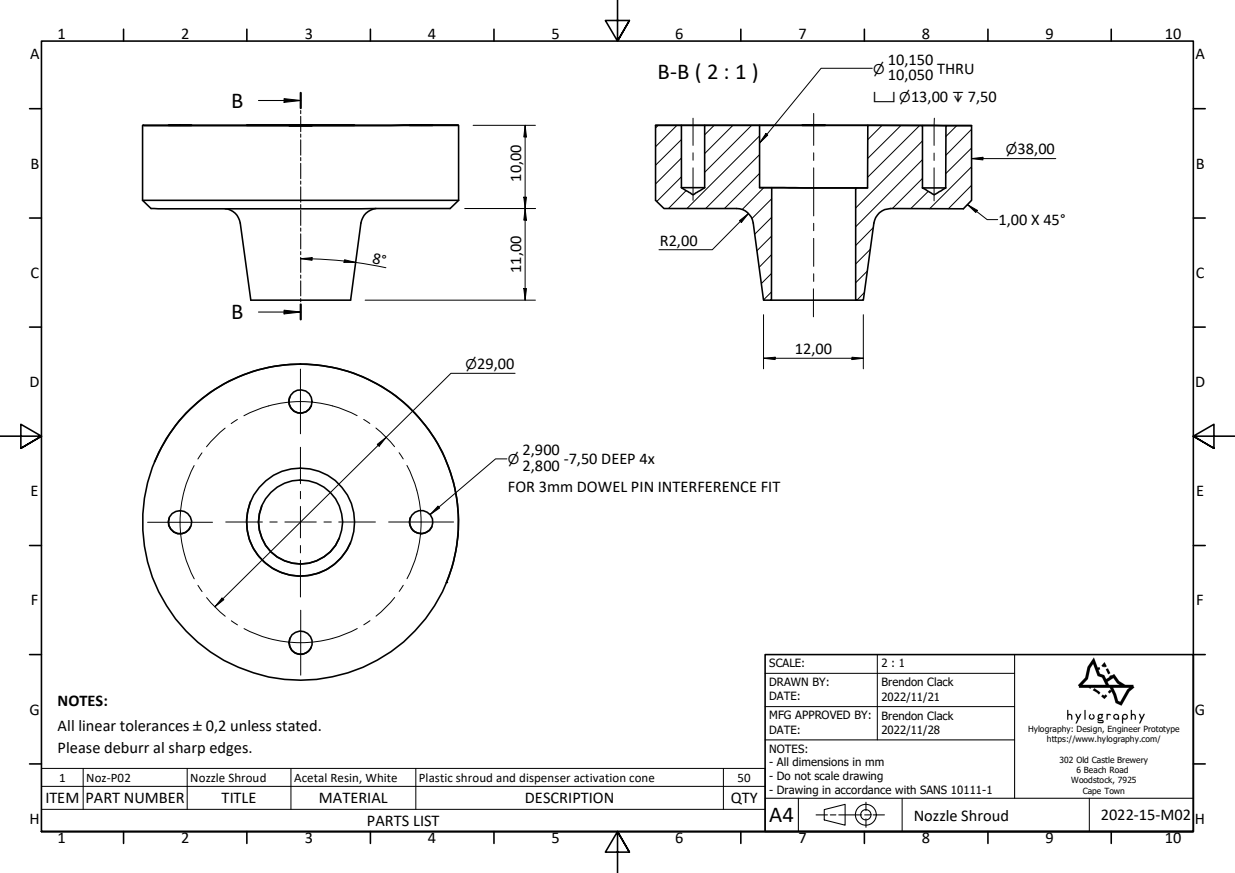
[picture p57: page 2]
PARTS LIST; Nozzle Shroud; -7,50 DEEP 4x

FOR 3mm DOWEL PIN INTERFERENCE FIT

DRAWN BY: DATE: | Brendon Clack 2022/11/21

NOTES:
All linear tolerances `0,2 unless stated.
Please deburr al sharp edges.

MFG APPROVED BY: DATE: | Brendon Clack 2022/11/28

Hylography: Design, Engineer Prototype
https://www.hylography.com/

- All dimensions in mm
- Do not scale drawing
- Drawing in accordance with SANS 10111-1

302 Old Castle Brewery
6 Beach Road
Woodstock, 7925
Cape Town

1 | Noz-P02 | Nozzle Shroud | Acetal Resin, White | Plastic shroud and dispenser activation cone | 50
ITEM | PART NUMBER | TITLE | MATERIAL | DESCRIPTION | QTY

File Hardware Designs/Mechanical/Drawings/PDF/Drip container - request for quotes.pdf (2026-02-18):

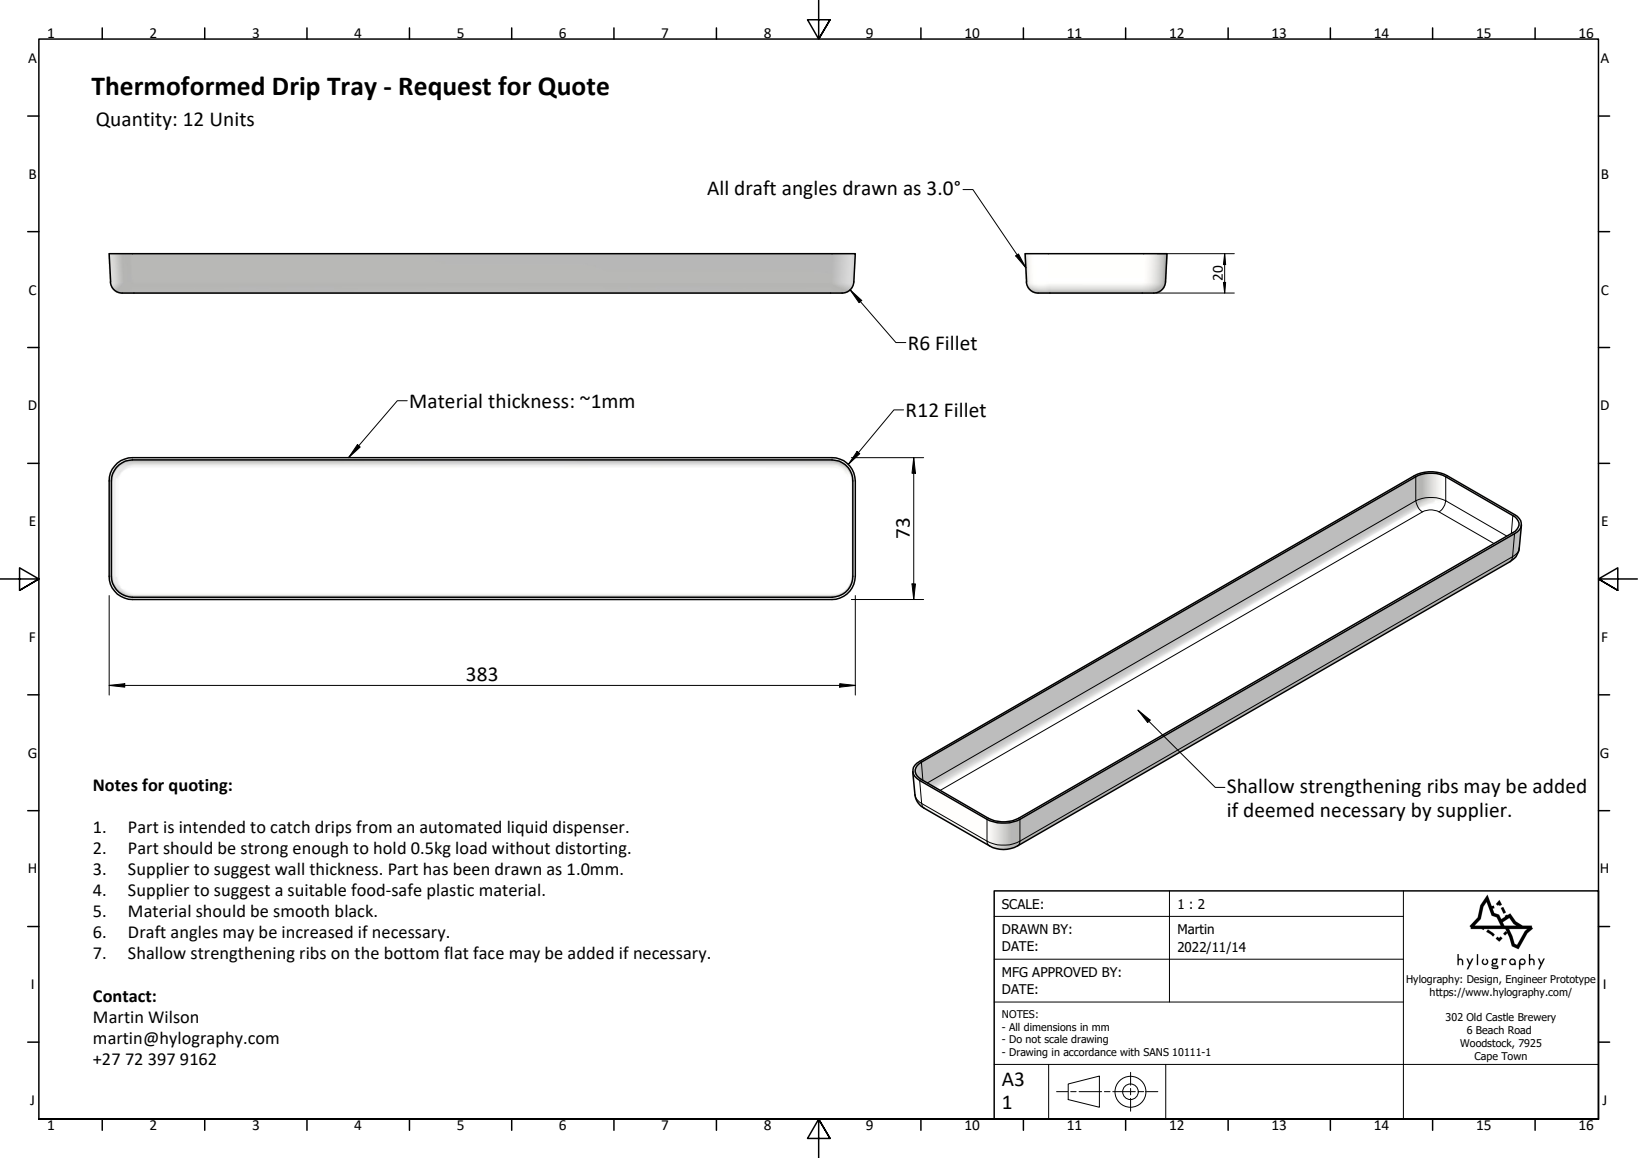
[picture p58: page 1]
R12 Fillet; R6 Fillet; Material thickness: ~1mm

Thermoformed Drip Tray - Request for Quote
Quantity: 12 Units

All draft angles drawn as 3.0°

Notes for quoting:

Shallow strengthening ribs may be added
if deemed necessary by supplier.

1. Part is intended to catch drips from an automated liquid dispenser.
2. Part should be strong enough to hold 0.5kg load without distorting.
3. Supplier to suggest wall thickness. Part has been drawn as 1.0mm.
4. Supplier to suggest a suitable food-safe plastic material.
5. Material should be smooth black.
6. Draft angles may be increased if necessary.
7. Shallow strengthening ribs on the bottom flat face may be added if necessary.

SCALE: | 1 : 2 | Hylography: Design, Engineer Prototype https://www.hylography.com/302 Old Castle Brewery 6 Beach Road Woodstock, 7925 Cape Town

DRAWN BY: DATE: | Martin 2022/11/14

MFG APPROVED BY: DATE:

Contact:
Martin Wilson
martin@hylography.com

NOTES:
- All dimensions in mm
- Do not scale drawing
- Drawing in accordance with SANS 10111-1

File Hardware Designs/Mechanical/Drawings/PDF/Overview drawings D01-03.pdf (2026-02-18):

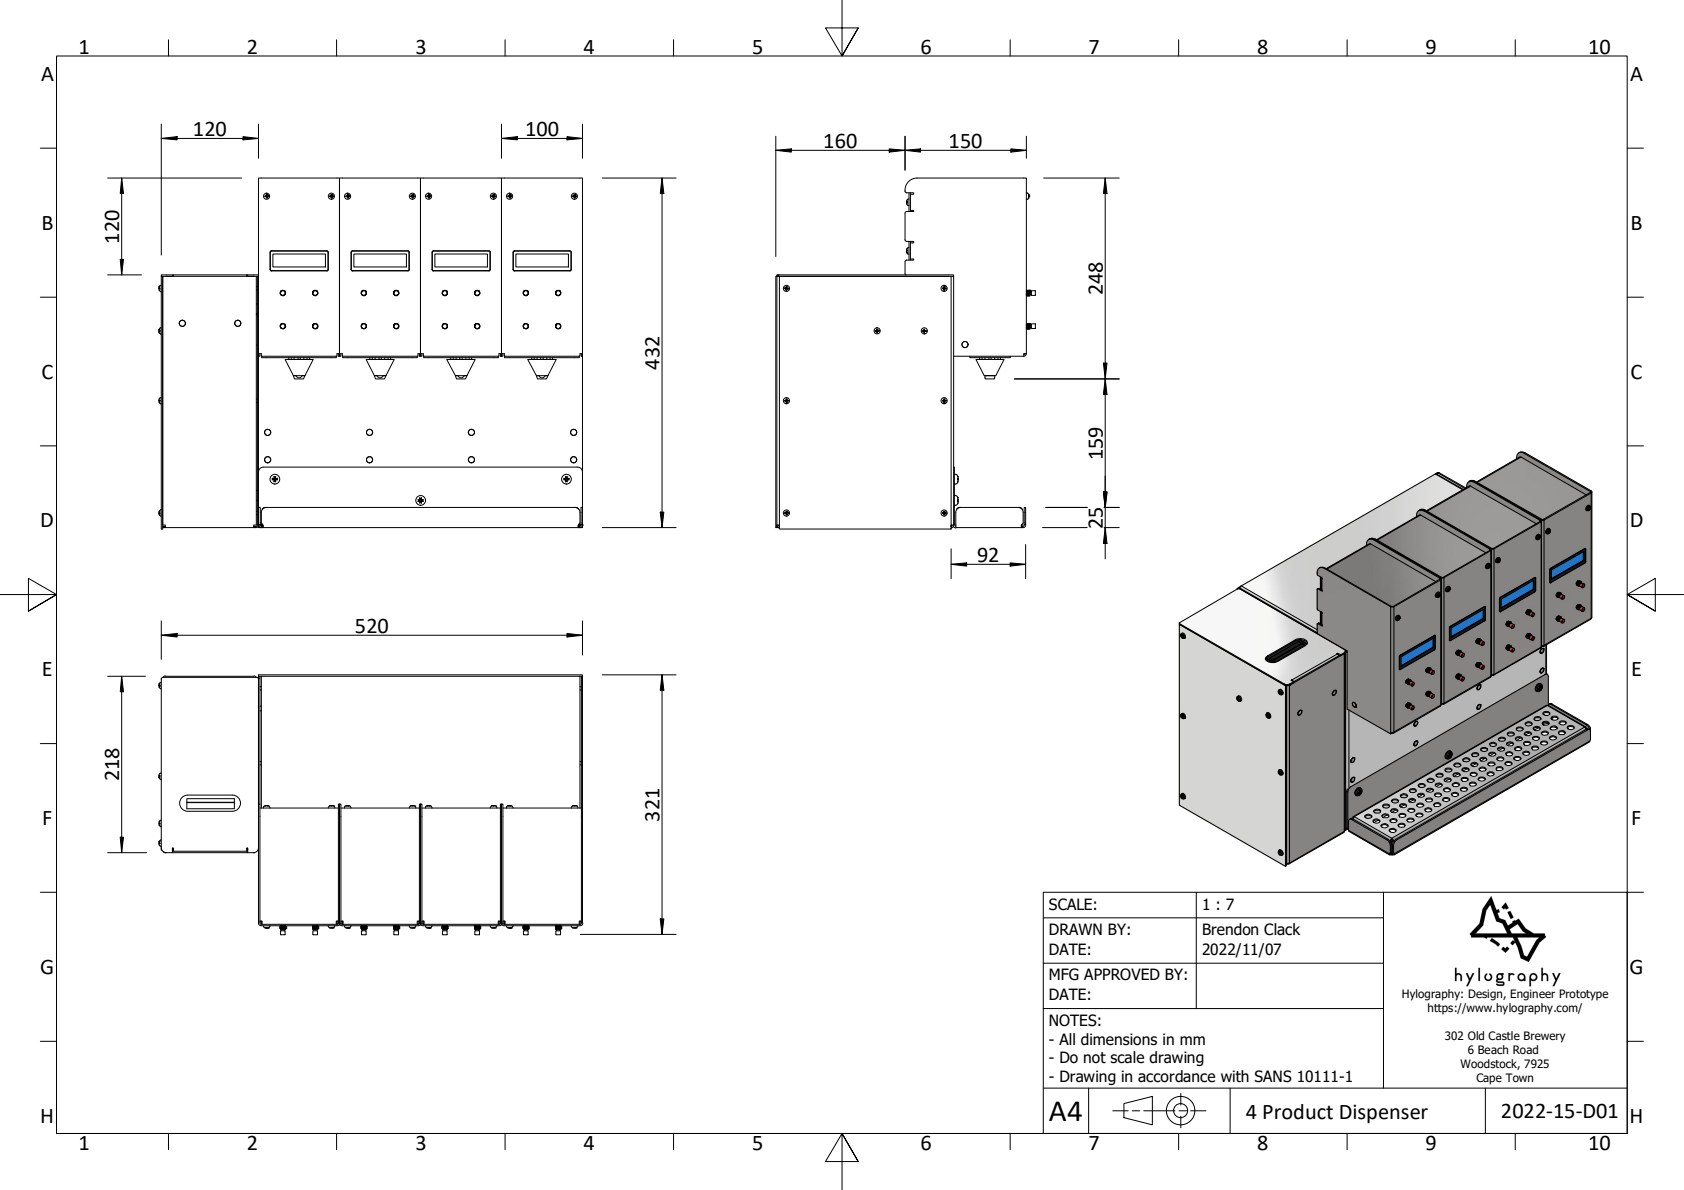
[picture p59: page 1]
4 Product Dispenser

DRAWN BY: DATE: | Brendon Clack 2022/11/07

MFG APPROVED BY: DATE:

Hylography: Design, Engineer Prototype
https://www.hylography.com/

NOTES:
- All dimensions in mm
- Do not scale drawing
- Drawing in accordance with SANS 10111-1

302 Old Castle Brewery
6 Beach Road
Woodstock, 7925
Cape Town

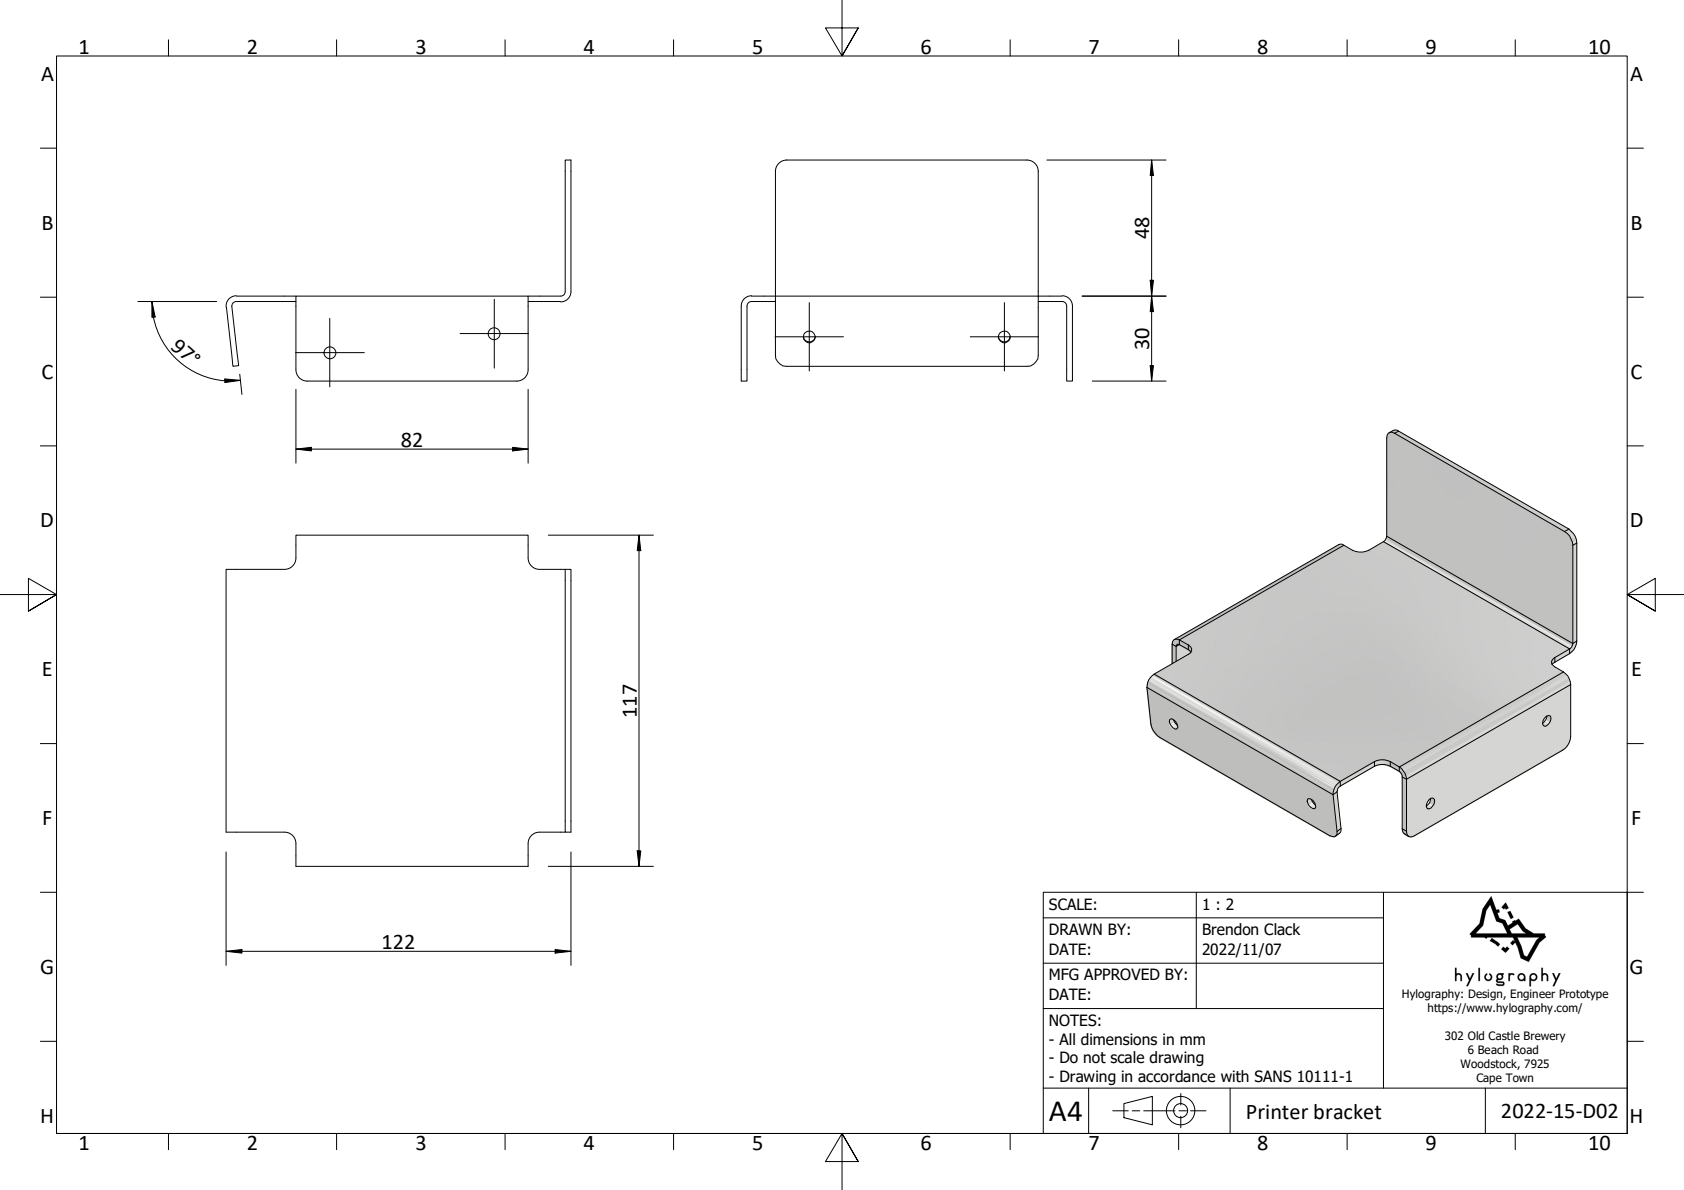
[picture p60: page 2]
Printer bracket

DRAWN BY: DATE: | Brendon Clack 2022/11/07

MFG APPROVED BY: DATE:

Hylography: Design, Engineer Prototype
https://www.hylography.com/

NOTES:
- All dimensions in mm
- Do not scale drawing
- Drawing in accordance with SANS 10111-1

302 Old Castle Brewery
6 Beach Road
Woodstock, 7925
Cape Town

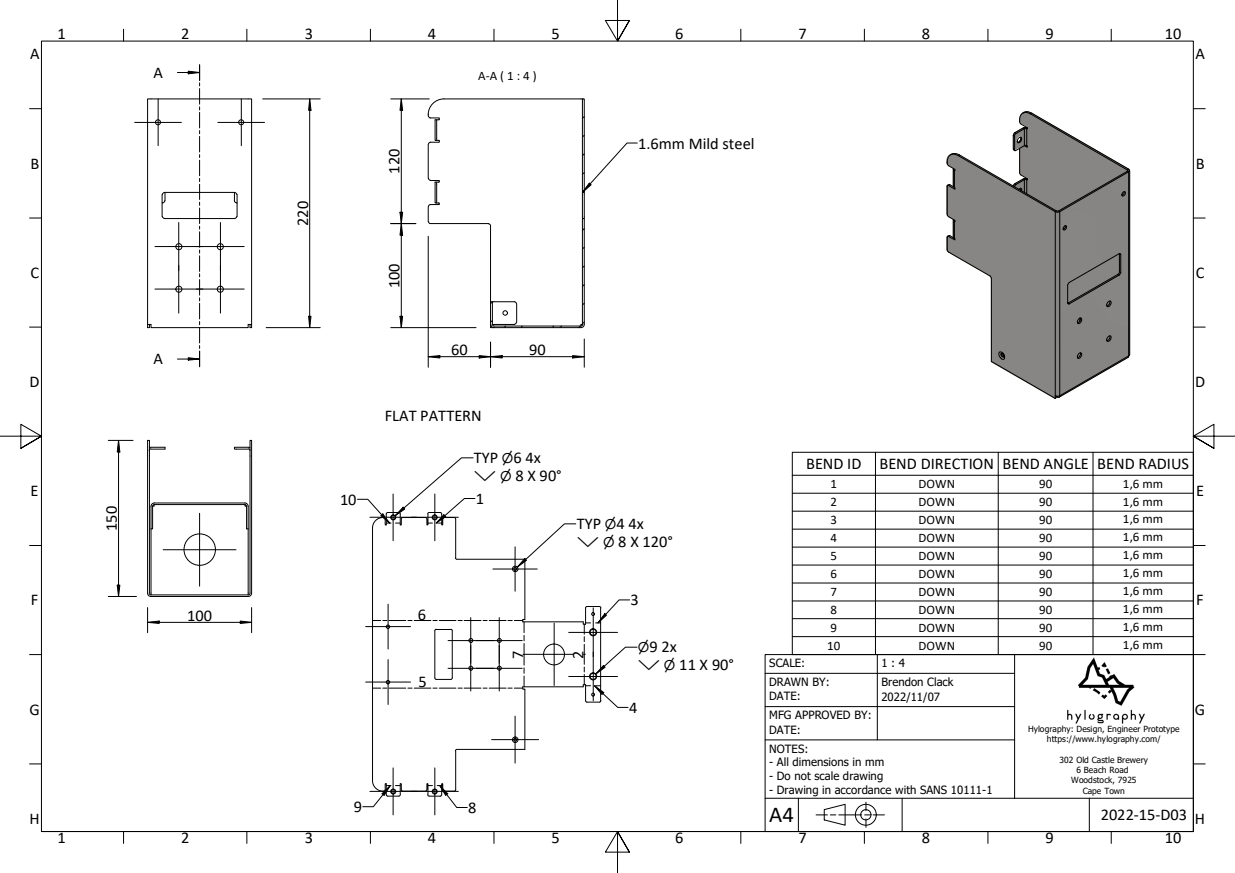
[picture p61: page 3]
DOWN; TYP ⌀4 4x ⌵ ⌀ 8 X 120°; TYP ⌀6 4x ⌵ ⌀ 8 X 90°; FLAT PATTERN; 1.6mm Mild steel

BEND ID | BEND DIRECTION | BEND ANGLE | BEND RADIUS
1 | DOWN | 90 | 1,6 mm
2 | DOWN | 90 | 1,6 mm
3 | DOWN | 90 | 1,6 mm
4 | DOWN | 90 | 1,6 mm
5 | DOWN | 90 | 1,6 mm
6 | DOWN | 90 | 1,6 mm
7 | DOWN | 90 | 1,6 mm
8 | DOWN | 90 | 1,6 mm
9 | DOWN | 90 | 1,6 mm

DRAWN BY: DATE: | Brendon Clack 2022/11/07

MFG APPROVED BY: DATE:

Hylography: Design, Engineer Prototype
https://www.hylography.com/

NOTES:
- All dimensions in mm
- Do not scale drawing
- Drawing in accordance with SANS 10111-1

302 Old Castle Brewery
6 Beach Road
Woodstock, 7925
Cape Town

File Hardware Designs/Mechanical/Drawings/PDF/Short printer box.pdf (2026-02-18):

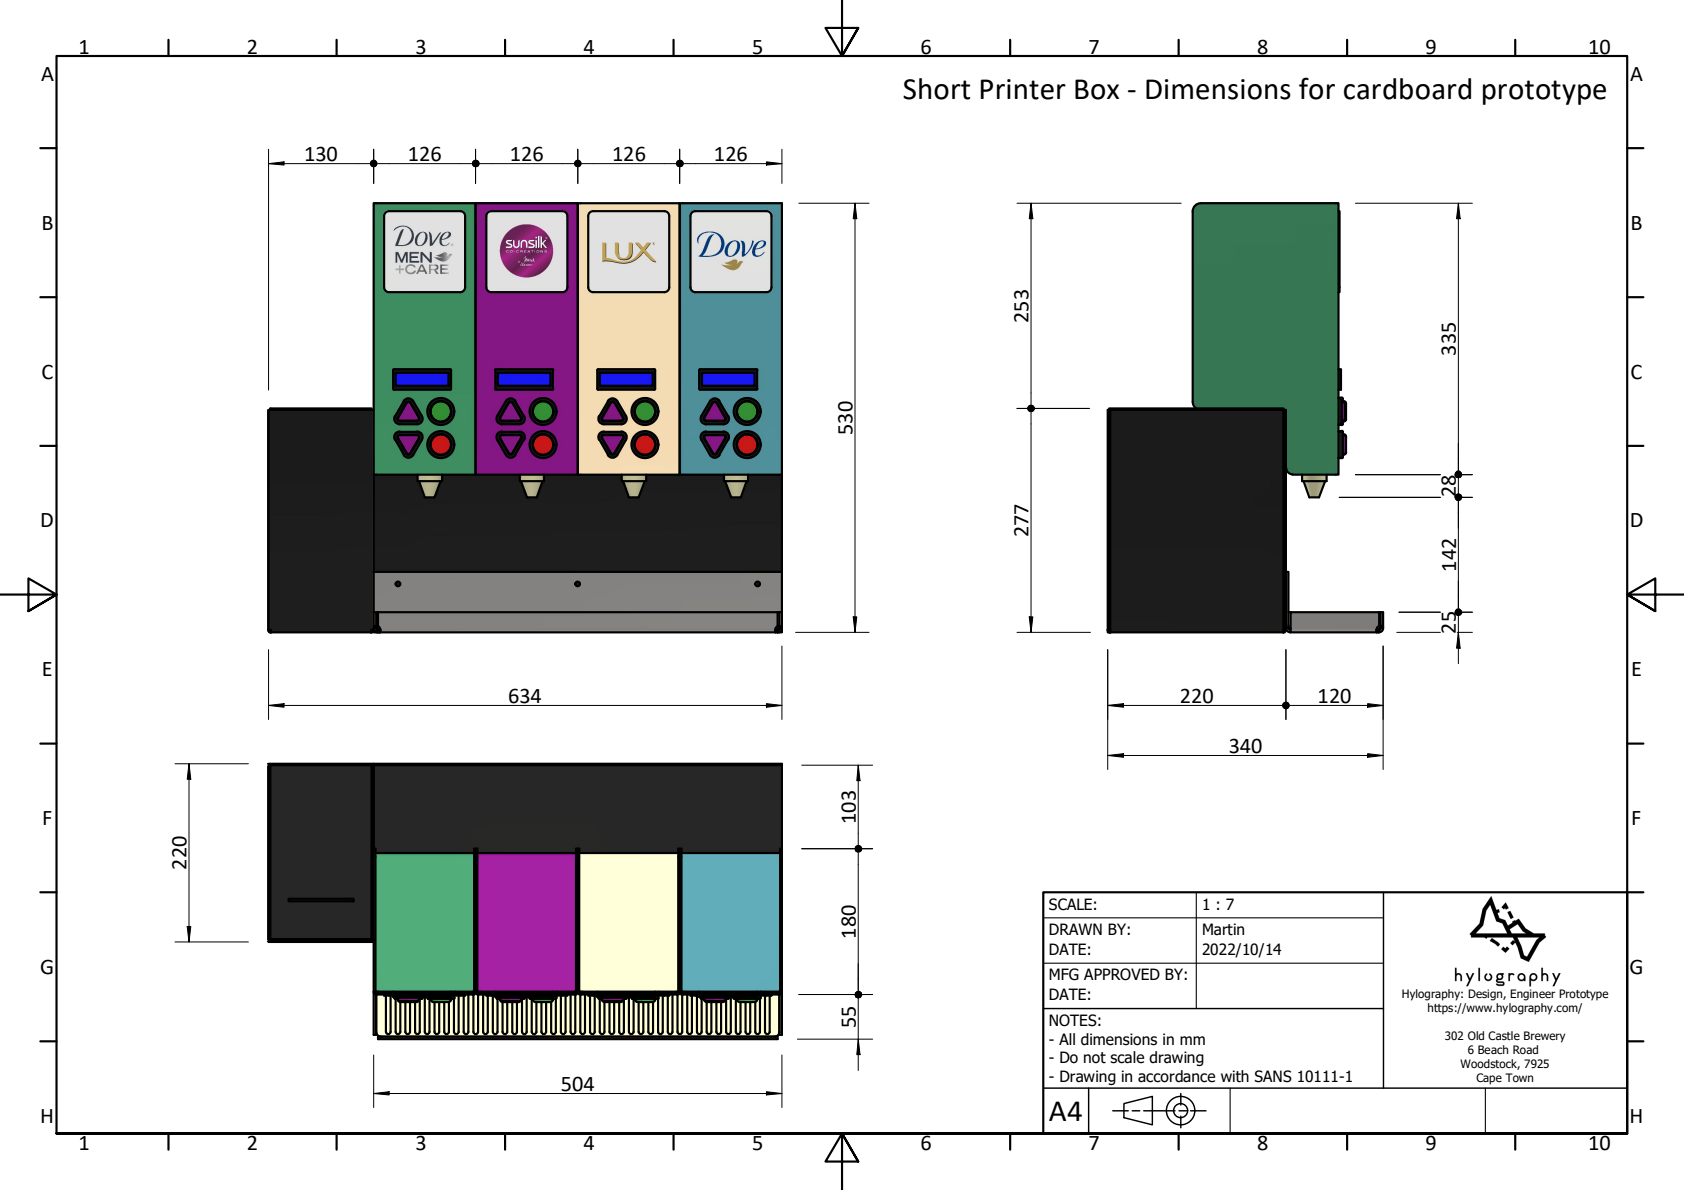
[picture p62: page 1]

Short Printer Box - Dimensions for cardboard prototype

DRAWN BY: DATE: | Martin 2022/10/14

MFG APPROVED BY: DATE:

Hylography: Design, Engineer Prototype
https://www.hylography.com/

NOTES:
- All dimensions in mm
- Do not scale drawing
- Drawing in accordance with SANS 10111-1

302 Old Castle Brewery
6 Beach Road
Woodstock, 7925
Cape Town

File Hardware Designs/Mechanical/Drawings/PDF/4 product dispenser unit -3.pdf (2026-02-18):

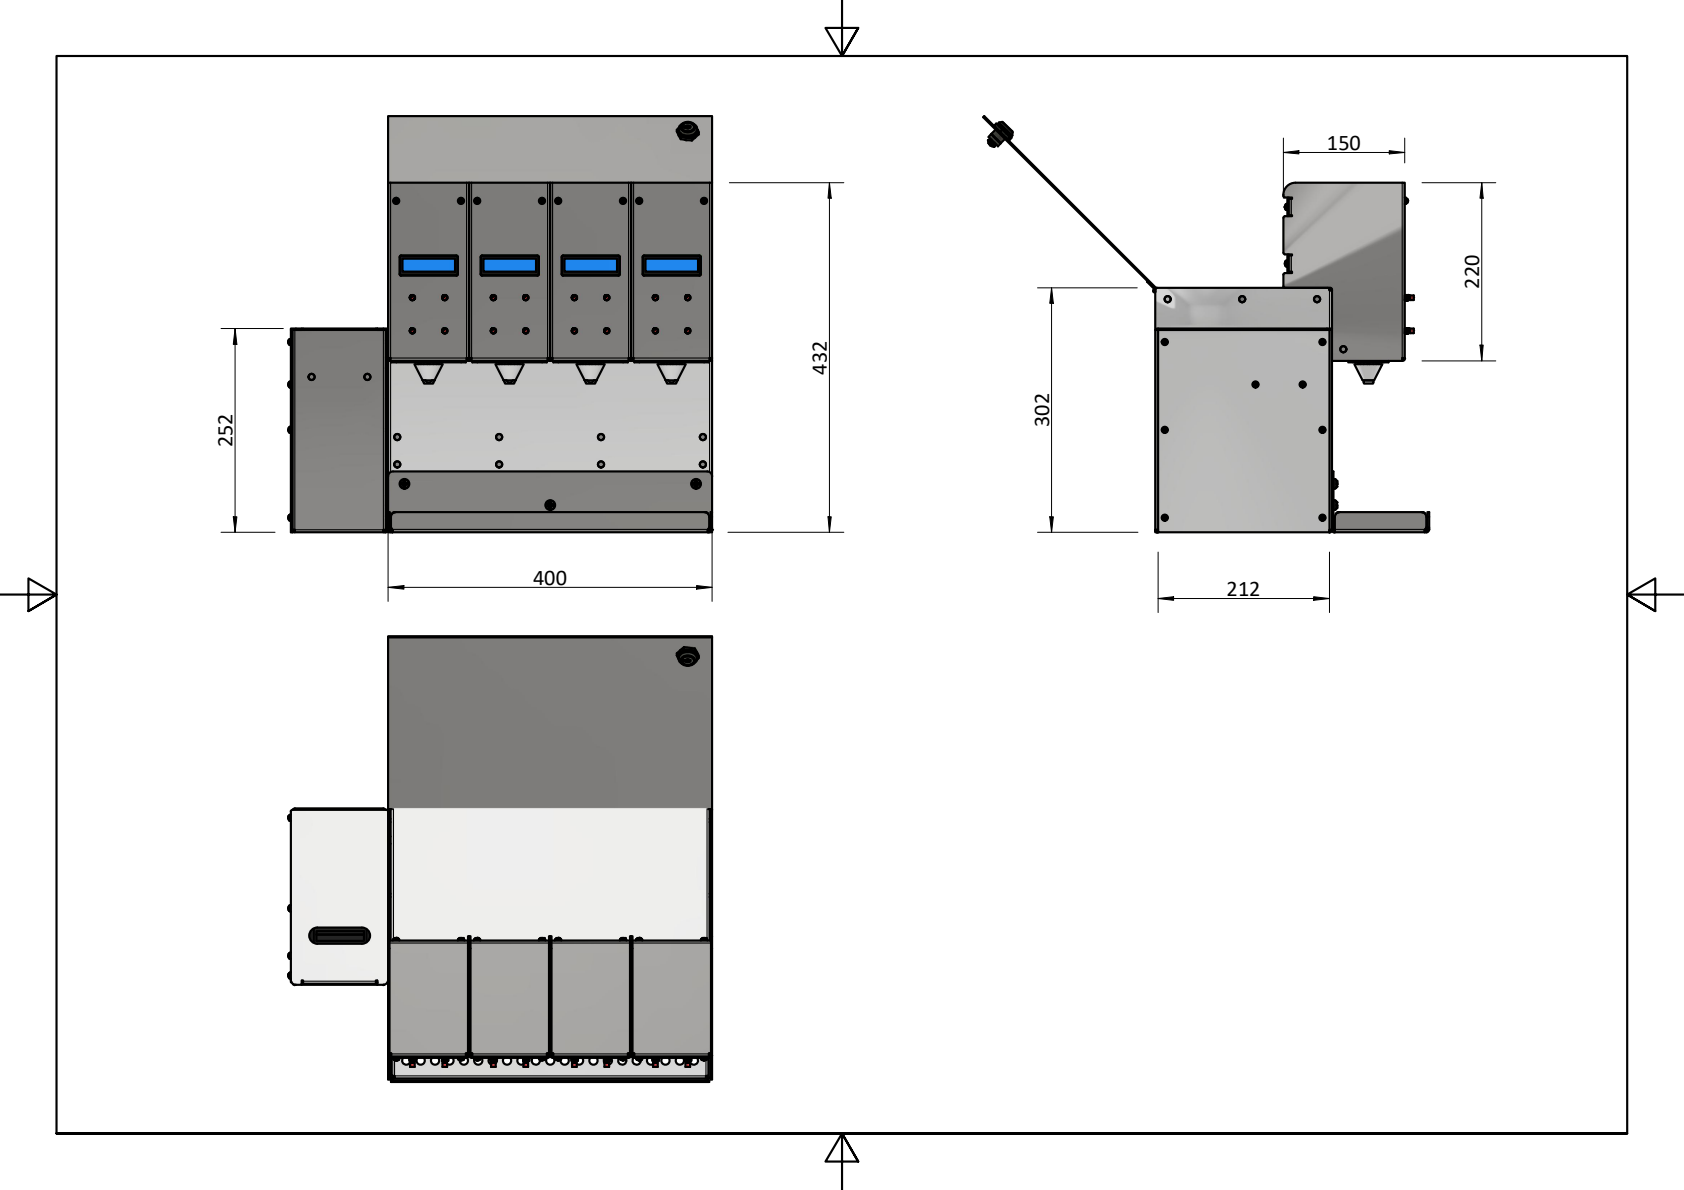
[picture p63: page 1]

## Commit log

2026-03-31 Rename Dispenser Final BOM (2).xlsx to BoM.xlsx
    [BoM.xlsx]
2026-03-31 Rename BoM.xlsx to Bill of Materials.xlsx
    [Bill of Materials.xlsx]
